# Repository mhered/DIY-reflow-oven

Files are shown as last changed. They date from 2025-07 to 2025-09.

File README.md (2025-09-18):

# DIY reflow oven

Inspired in [this video](https://www.youtube.com/watch?v=asZ1zhef8Ss) (see also the [blog post](https://www.digikey.com/en/maker/projects/how-to-build-a-solder-reflow-oven/6c52df4782084f8d97c62d1349df058f)), but I thought the BOM was too expensive. I used also [this video](https://www.youtube.com/watch?v=k9xzGO0SVg0) as inspiration, which discusses temperature curves, and includes a custom controller PCB.

Bought the following elements instead:

| Qty  | Item | Image | Description | Link | Pack Price (€) | Pack Size | Unit Price (€) | Subtotal (€) |
| ---- | --- | --- | --- | --- | --- | --- | --- | --- |
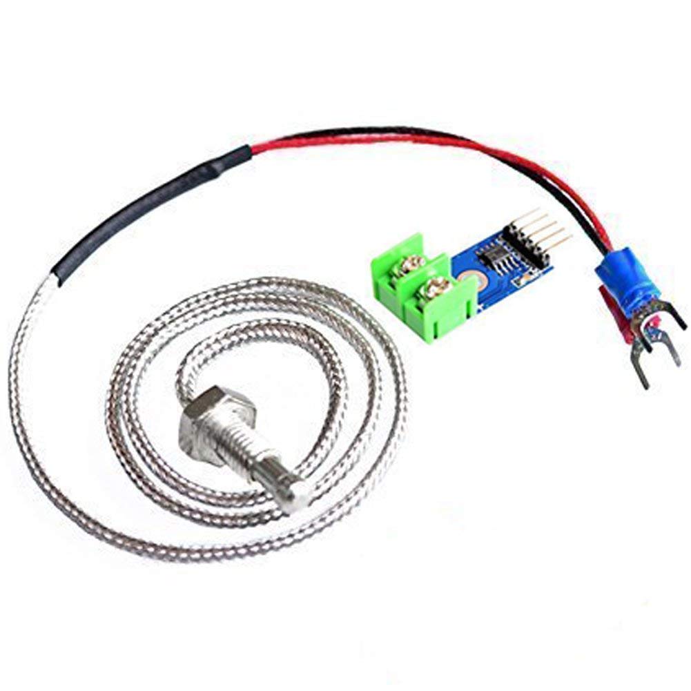
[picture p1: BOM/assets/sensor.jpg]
| 1 | [ARCELI MAX6675 module + K-type thermocouple](./BOM/sensor.md) |  | K-type thermocouple module with MAX6675, 0–600 °C range, SPI output | [Amazon](https://www.amazon.es/dp/B07MY36P9Y) | 7.99 | 1 | 7.99 | 7.99 |
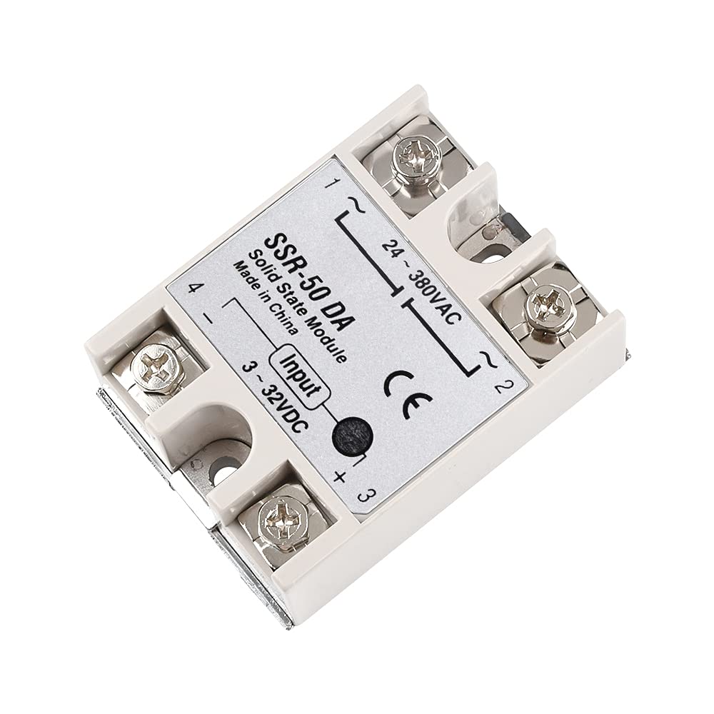
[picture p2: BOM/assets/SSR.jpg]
| 1 | [SSR-50DA Solid State Relay](./BOM/ssr.md) |  | DC 3–32 V input, AC 24–380 V output, 50A max, for heater control | [Amazon](https://www.amazon.es/dp/B08FX1DDJM) | 9.59 | 1 | 9.59 | 9.59 |
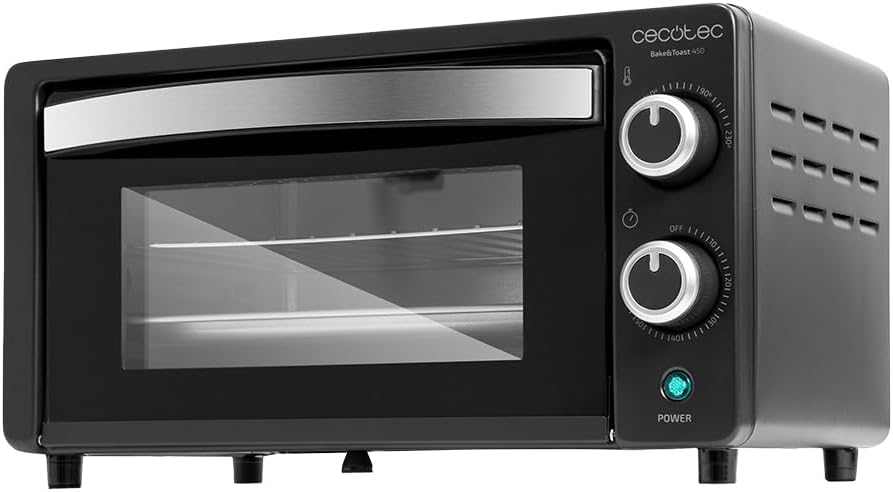
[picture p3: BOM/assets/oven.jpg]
| 1 | [Cecotec Bake&Toast 1090 Oven](./BOM/oven.md) |  | 10 L tabletop oven, 1000 W, 60 min timer, up to 230 °C | [Amazon](https://www.amazon.es/dp/B0BQ13YSVT) | 31.90 | 1 | 31.90 | 31.90 |
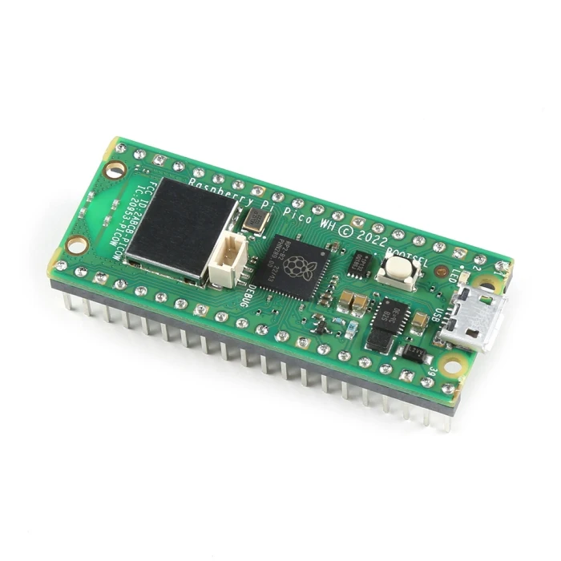
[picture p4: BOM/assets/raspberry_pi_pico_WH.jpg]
| 1 | [Raspberry Pi Pico WH](BOM/RPi_Pico.md) |  | | | | | | |
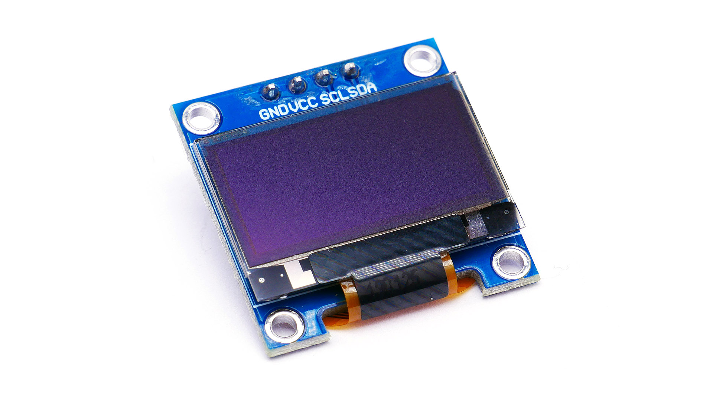
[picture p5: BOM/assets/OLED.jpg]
| 1 | [SSD1306 OLED](./BOM/OLED.md) |  | | | | | | |

I already had the Raspberry Pico WH and SSD1306 OLED screen laying around.

See [BOM/RPi_Pico.md](BOM/RPi_Pico.md) for  instructions on how to flash micropython on to the Raspberry Pi Pico and details of the pinout.

## Step 1 - Measure temperature and show it on the OLED

Target: display the temperature on the OLED using a MicroPython script

Inspired in this source video: https://www.youtube.com/watch?v=aUPvASe8D-w

### Wiring

While I wait for the thermocouple to arrive by post I am building a proof of concept using a 10K thermistor and a 10kOhms resistor from my trusted [Freenove_Ultimate_Starter_Kit_for_Raspberry_Pi](https://github.com/Freenove/Freenove_Ultimate_Starter_Kit_for_Raspberry_Pi), wired in a voltage divider configuration as shown below (actually one of the tutorials in this repo demonstrates this application).

```
3.3V --- [10kΩ] ---+--- [10K Thermistor] --- GND
                   |
                GPIO26 (ADC 0)
```

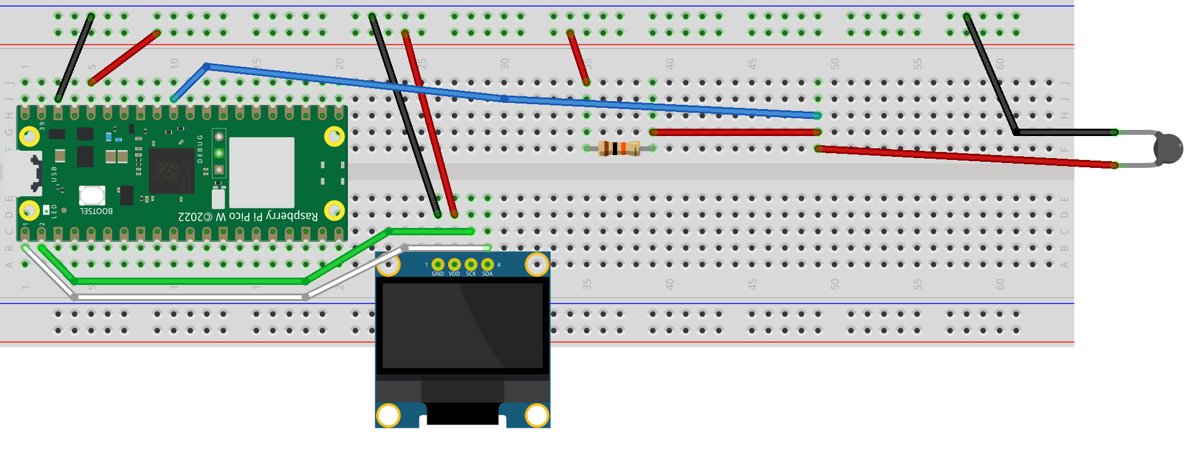
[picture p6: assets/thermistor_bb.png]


Check out the [fritzing model](./fritzing/diy_reflow_oven_v1.fzz)

### Firmware

* `main.py` - main function
* `display.py` - functions to send info to the OLED display  
* `thermistor.py` -  functions to read the sensor. Note I used a very simplified model of the variation of the thermistor's resistance with temperature using a single constant. This [Online Steinhart-Hart model coefficients calculator]( https://www.thinksrs.com/downloads/programs/therm%20calc/ntccalibrator/ntccalculator.html) provides a more accurate model but requires making R measurements at 3 known T points, which I felt was an overkill for the proof of concept.

Copy dependencies to the Pico:

* `ssd1306.py` - library to communicate with the OLED (copied from https://github.com/stlehmann/micropython-ssd1306)
* `writer.py` - an interpreter for custom fonts for the OLED  (copied from the link in the comments of this video: https://www.youtube.com/watch?v=bLXMVTTPFMs)
* `freesans20.py` - a custom large font for the OLED  (copied from the link in the comments of this video: https://www.youtube.com/watch?v=bLXMVTTPFMs)

Note: the files from https://github.com/peterhinch/micropython-font-to-py did not work for me.

## Step 2  - setup a web server over WiFi to interact from computer or phone

Profiting from the capabilities of the RPi Pico I decided to set up a local web server over Wifi to view temperature readings from a computer or phone connected to the same Wifi network as the Pico

### Firmware

* `wifi.py` : function to connect the RPi Pico to Wifi. Requires uploading to the Pico a `secrets.py` file containing the network information as follows:

```bash
SSID = "Network"
PASSWORD = "Password"
```

* `server.py` :  a very basic web server that just publishes the temperature every 2 seconds

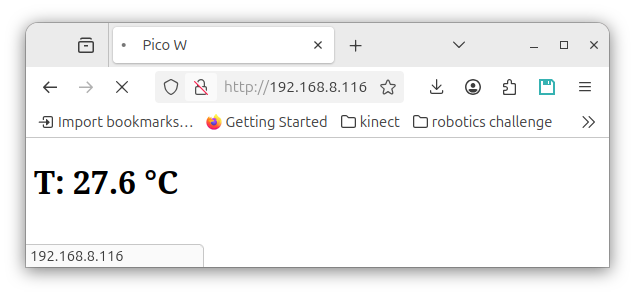
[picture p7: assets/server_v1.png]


## Step 3 - Control the heater

Next we refactor using the [Microdot](https://github.com/miguelgrinberg/microdot) framework and add a few improvements:

* Replace repeated full-page reload every 2 seconds using meta-refresh with polling a tiny JSON file using Java Script. This is more efficient, avoids page flicker and is more extensible 
* Save web page as static files (`index.html` and `style.css`) with a minimalistic, modern design
* Add `/set_target?value=XX` route to update target temperature via HTTP
* Add REST endpoint `/temperature` exposing current and target temp + heater state

* `heater.py` - contains the target temperature logic and functions to control a heater in GPIO22

Dependencies: copy the library  `microdot.py` to the pico

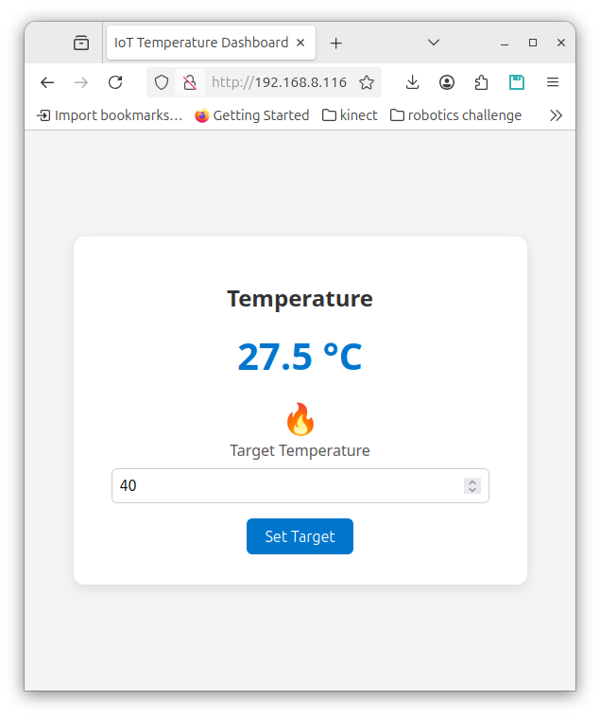
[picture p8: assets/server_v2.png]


### Wiring

In preparation to control the heater we add an LED on GPIO22

Check out the [fritzing model](./fritzing/diy_reflow_oven_v2.fzz)

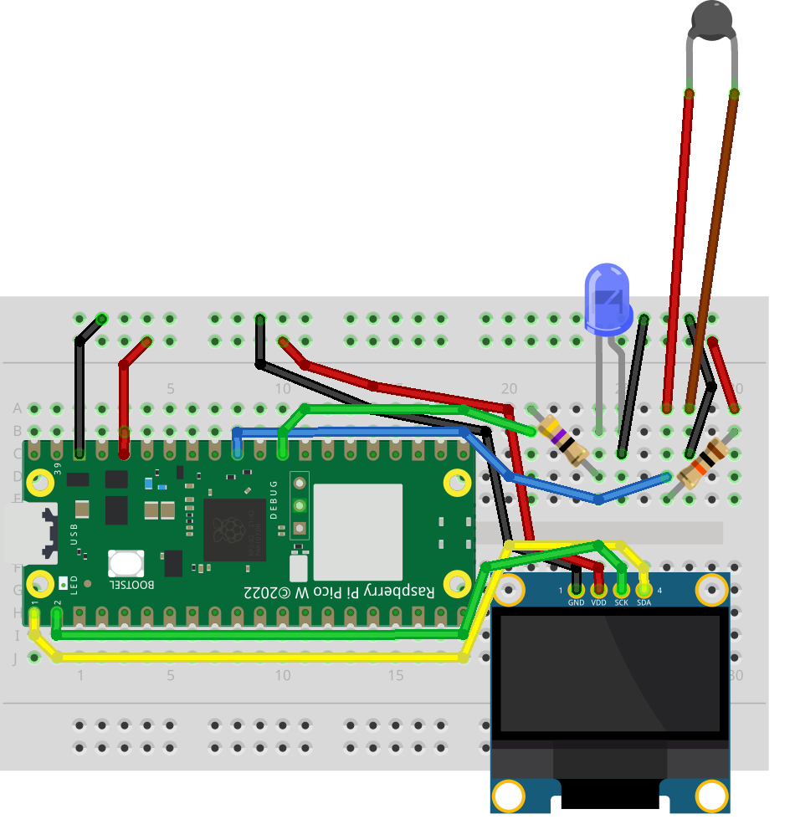
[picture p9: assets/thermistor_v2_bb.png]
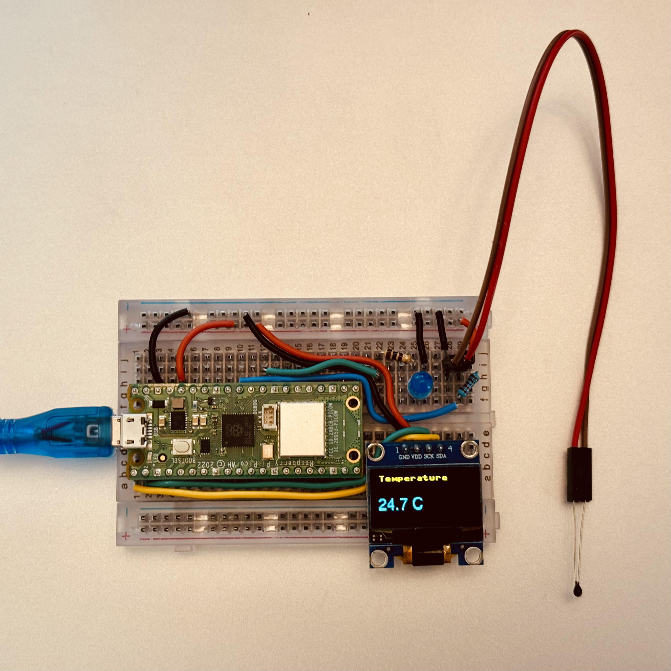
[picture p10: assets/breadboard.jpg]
|  |  |
| --- | --- |

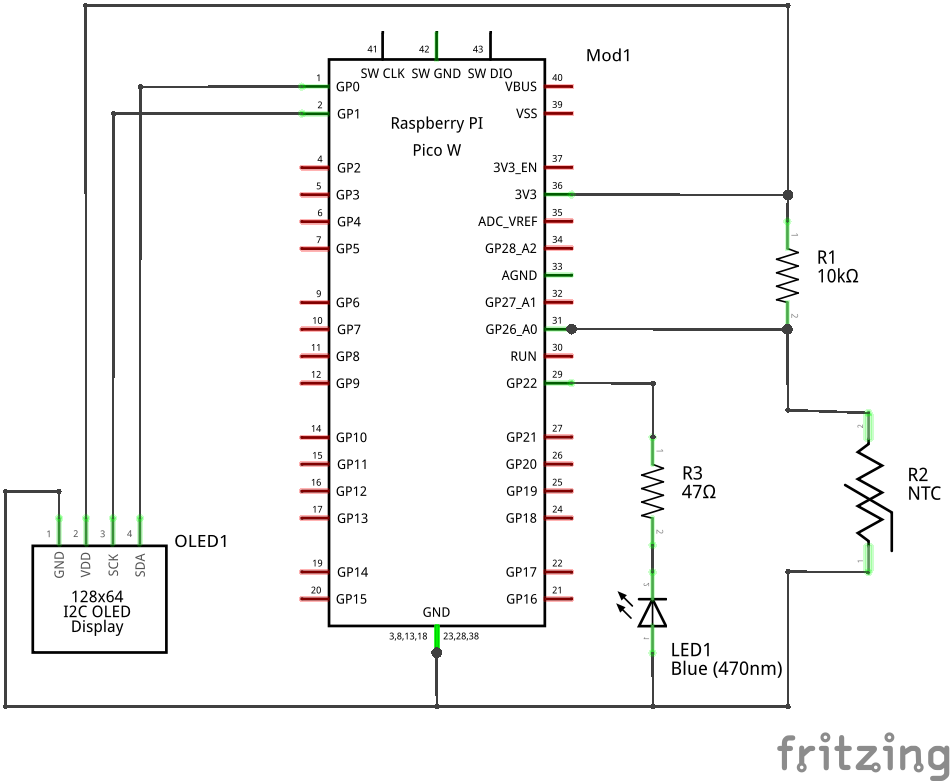
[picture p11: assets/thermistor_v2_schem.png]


## Step 4 - Temperature Profiles

Next we refactor to add support for temperature profiles and disable manual target temperature setting:

- `profile.py` - classes for multi-phase temperature control with JSON serialization
- `profile_manager.py` functions to manage profile execution, file persistence, and state tracking
- new `profiles/` folder to store temperature profiles as JSON files
  - [low_temp.json](./src/profiles/low_temp.json) profile based on [this datasheet](./assets/low_temp_solder_paste_datasheet.pdf) for Sn42Bi57Ag1 Low Temperature Solder Paste

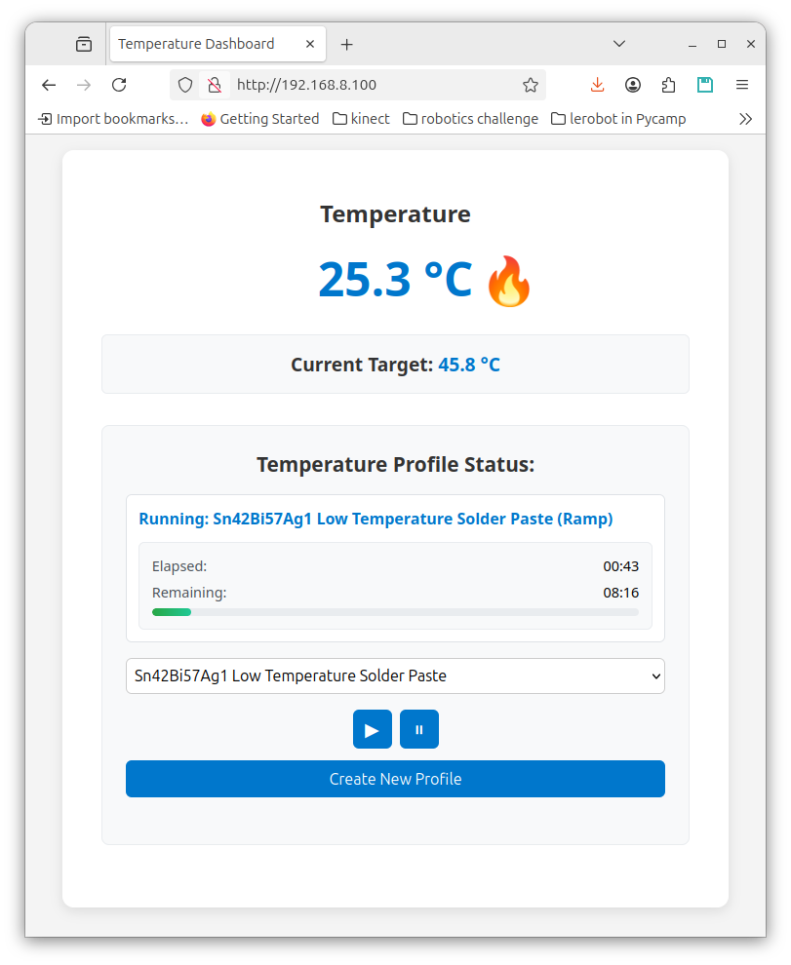
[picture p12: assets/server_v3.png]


## Step 5 - Plot temperature graphs

This is a test with simulated temperature

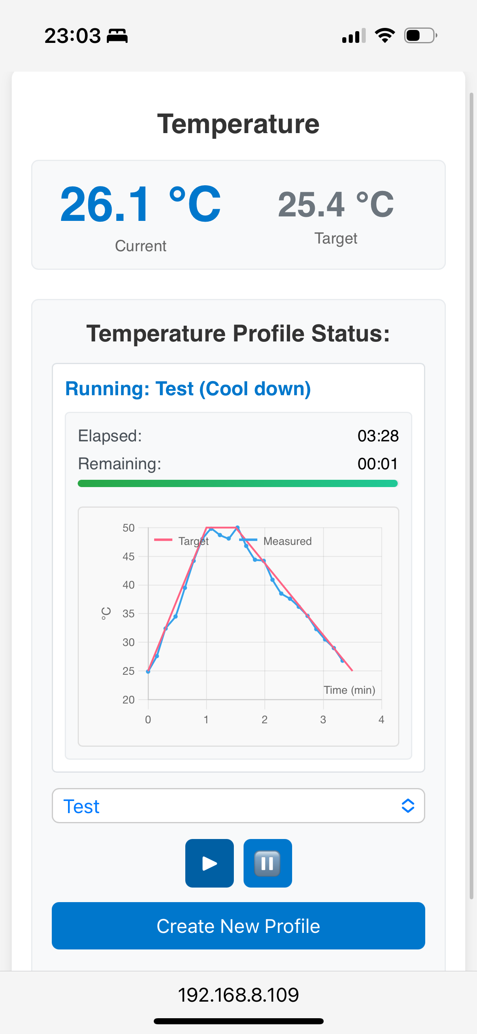
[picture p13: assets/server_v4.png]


## Step 5 - Optimize architecture

Move state logic to `ProfileManager` class, put some order in the UI, improve set of example profiles etc.

**Bulb Test 55 °C — Proof of Concept**

The graph below shows a temperature profile recorded during a full system test in a simple proof-of-concept setup. An old incandescent bulb served as the heating element, switched by the Raspberry Pi Pico via a solid-state relay connected to GPIO22 . To mimic an oven enclosure, the bulb and temperature sensor were covered with an inverted beer glass, allowing the air temperature to rise quickly to the 55 °C target.

The small ripples in the measured temperature trace reflect the heater control loop cycling the bulb on and off to follow the requested profile. Towards the end of the test, the measured temperature fell behind the target curve because heat dissipation under the glass was not fast enough to achieve the desired cooling rate.

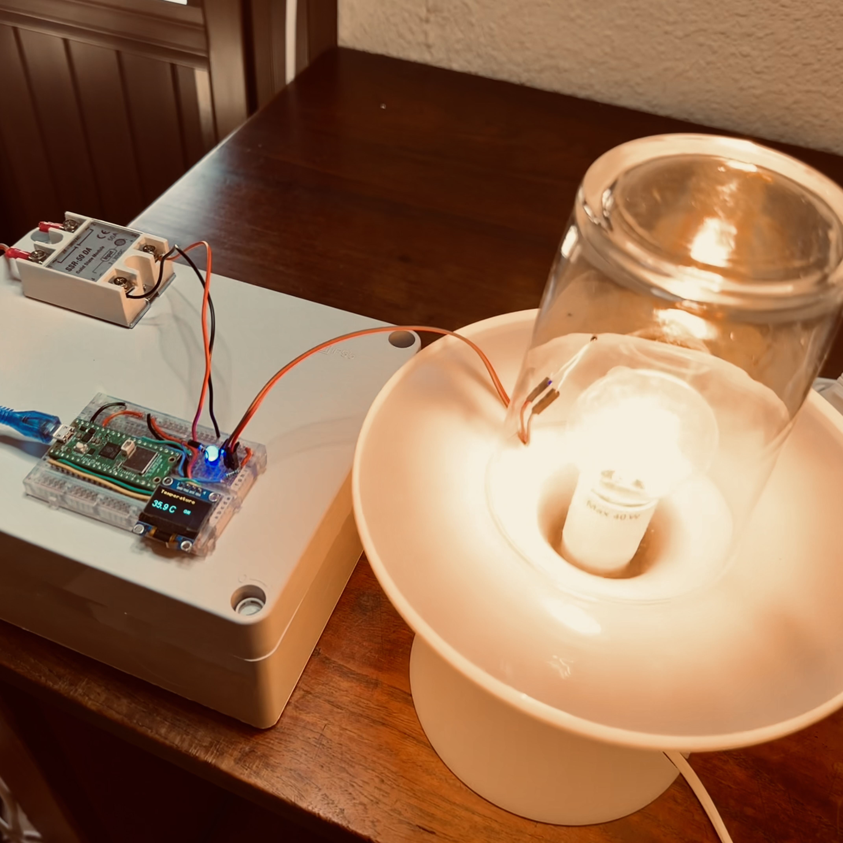
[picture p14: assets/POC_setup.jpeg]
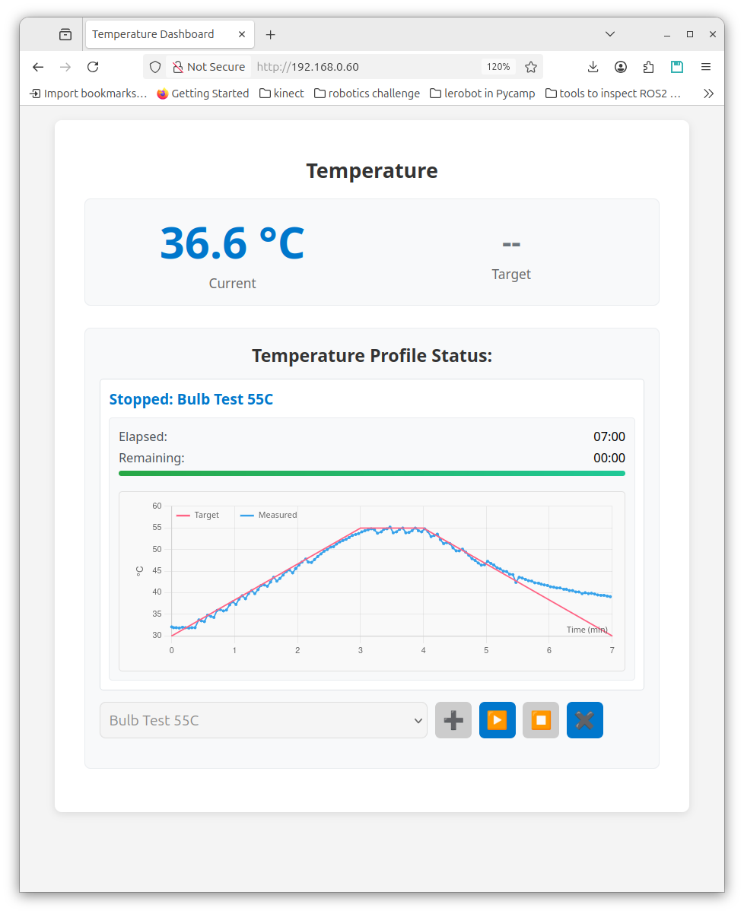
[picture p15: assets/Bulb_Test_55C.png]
|  |  |
| --- | --- |

## Step 6 - (Finally) hacking the oven for real

Two sanity checks on the Cecotec oven before we proceed:

1. Two infrared heater pieces powerful enough (1000W) to quickly heat up and cool down
2. Confirmed that if we shut down and power up again the oven it resumes working (there are no electronics that reset the timer etc). This allows us controlling the oven as we did with the incandescent bulb in the proof of concept.
3. The lower tray for removing breadcrumbs is perfect to feed the wire of the thermocouple to get temperature measurements inside the oven without the need to drill a hole or modify the oven in any way.

### Firmware

Next we need to adapt the code for the K-type thermocouple and MAX6675. Refer to [this tutorial](https://www.electroniclinic.com/raspberry-pi-pico-and-max6675-based-industrial-temperature-monitoring-system/).

## WIP

- [ ] created branch `feature/polling-improvements-WIP` with partial implementation of incremental temperature updates instead of full dumps for the graph to enable higher refresh rates without memory problems, and to configure the refresh of different elements such as the graph, measured and target temperatures, UI buttons states, etc using centralized named constants instead of magic numbers scattered throughout the code
- [ ] check also open issues
- [x] test the oven and reflow first part
- [ ] add pictures and gifs

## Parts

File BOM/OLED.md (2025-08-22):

# SSD1306 OLED



SSD1306 is a popular controller for OLED screens

resolution 128x64

Check if the I2C address is 0x3D or 0x3C

Power consumption: according to https://bitbanksoftware.blogspot.com/2019/06/how-much-current-do-oled-displays-use.html,  for text (~50% pixels at 100%) is around 10mA so at 5V is ~50mW 

### Wiring the SSD1306 OLED to the Pico

I2C communication requires only 4 pins: GND, VCC, SDA, SCL 

| OLED Pin | Connect To Pico | Pico Pin Number | Function |
| --- | --- | --- | --- |
| `VCC` | 3.3V | Pin 36 | Power |
| `GND` | GND | Pin 38 or 3 | Ground |
| `SCK` | GP1 | Pin 2 | I²C0 SCL |
| `SDA` | GP0 | Pin 1 | I²C0 SDA |

## Controlling the OLED with Micropython

* `ssd1306.py` - library to communicate with the OLED (copied from https://github.com/stlehmann/micropython-ssd1306)

## Large fonts in Micropython

Ref. https://github.com/peterhinch/micropython-font-to-py 

* `writer.py` - an interpreter for custom fonts for the OLED
* `freesans20.py` - a custom large font for the OLED 

Note: the files from https://github.com/peterhinch/micropython-font-to-py did not work for me, so I copied them instead from the link in the comments of this video: https://www.youtube.com/watch?v=bLXMVTTPFMs

## Useful references

* A tool to design pixelart: https://www.pixilart.com/



* Check out wokwi online emulator https://wokwi.com/ for Arduino, ESP32 and Raspberry Pi Pico and animation maker https://animator.wokwi.com/

  Using the wokwi emulator I made code to display distance measurements, check:

  * parking_sensor: https://wokwi.com/projects/380210366387901441
  * distance_measurement: https://wokwi.com/projects/380210201131269121

* Check out also this image2cpp tool to make byte arrays from images and viceversa: http://javl.github.io/image2cpp/

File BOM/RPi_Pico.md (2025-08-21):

# Raspberry Pi Pico WH



### RPi Pico WH pinout



### Flashing MicroPython onto the Pico

I used [Thonny](https://thonny.org/) (a python IDE for beginners with great MicroPython integration). 

1. Install and run:

```bash
$ sudo apt install thonny
$ thonny
```

2. Plug the RPi Pico in boot mode: while holding down the **BOOTSEL** button on the RPi Pico, connect the USB cable to your computer, and a new drive will appear: **RPI-RP2**

3. flash MicroPython on the RPi Pico: 
   1. Go to **Tools** > **Options**
   2. In the **Interpreter** tab select **"MicroPython (Raspberry Pi Pico)"** in the dropdown and click **"Install or update MicroPython"**. Thonny will detect the RPi Pico automatically. 
   3. Select variant **"Raspberry Pi Pico W / Pico WH"**. It will download and flash the **MicroPython UF2 file** automatically.
   4. Click **Install** and wait for it to finish
   5. After install, the RPi Pico will reboot and connect directly to Thonny — you’ll see the MicroPython REPL (>>>) at the bottom.

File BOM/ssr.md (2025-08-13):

# diymore SSR-50 DA Solid State Relay

See: https://www.amazon.es/dp/B08FX1DDJM



Dimensions : ‎ 9,3 x 7,2 x 2,4 cm; 100 g
Manufacturer ‏ : ‎ diymore
ASIN ‏ : ‎ B08FX1DDJM
Manufacturer Reference ‏ : ‎ D010158

DC in: 3-32V DC

AC out: 24-380 VAC up to 50A

## References

Datasheets of similar products can be found [online](https://www.alldatasheet.com/datasheet-pdf/view/1940532/ETC/SSR50DA.html). I saved a local backup [here](../assets/SSR-40DA_datasheet.PDF).

A good reference: [Solid State Relay guide by phidgets](https://www.phidgets.com/docs/Solid_State_Relay_Guide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) 

According to **Practical Electronics by Inventors, sections 3.4.1 and 3.4.2** protecting tyhe Piuco with a diode seems unnecessary for my application, but also harmless. I decided to install a 1N4007. 

On the other hand it may be a good idea to add also a [plastic cover](https://es.aliexpress.com/item/1005002904930594.html) and a [heat sink]()

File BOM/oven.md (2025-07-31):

#   Cecotec Bake&Toast 1090 Oven

  

10 L tabletop oven, 1000 W, 60 min timer, up to 230 °C 

Source: https://www.amazon.es/dp/B0BQ13YSVT

Color	Negro
Dimensiones del producto	27f. x 37an. x 20,5al. cm, 2.77kg
Función especial	Termostato ajustable, temporizador
Tipo de control	Control por botones
Componentes incluidos	Bandeja para hornear, parrilla y asa con pinzas

Número de modelo	‎03816

[Manuals (PDF)](Cecotec_bake&toast_1090_manuals.pdf)

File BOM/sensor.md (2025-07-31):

#  ARCELI MAX6675 module + K-type thermocouple

  K-type thermocouple module with MAX6675, 0–600 °C range, SPI output  Source: https://www.amazon.es/dp/B07MY36P9Y

## Specs

**Manufacturer:** ARCELI  
**ASIN:** B07MY36P9Y  
**Dimensions:** 1.5 × 1.5 × 1.5 cm; 20 g

**Included:**

- 1× Sainsmart MAX6675 breakout module  
- 1× Sainsmart K-type thermocouple probe  
- 1× Sainsmart DuPont jumper cable set  

### MAX6675

- **Power Supply Voltage:** 3 V – 5 V DC  
- **Current Consumption:** 50 mA  
- **Interface Pins:** `GND`, `VCC`, `SCK`, `CS`, `SO` (SPI communication)  
- **Module Size:** 25 mm × 15 mm  
- **ESD Protection:** 2000 V signal-level protection  
- **Operating Temperature (board):** −20 °C to +85 °C  
- **Cold-Junction Compensation:** Built-in; automatically senses the temperature at the chip's own terminals and adjusts the thermocouple reading  
- **Break Detection:** Built-in thermocouple disconnection detection  

### Sensor

- **Thermocouple Type:** K-Type (nickel-chromium/nickel-alumel)  
- **Measurement Range:** 2 °C to 600 °C  
- **Temperature Resolution:** 0.25 °C

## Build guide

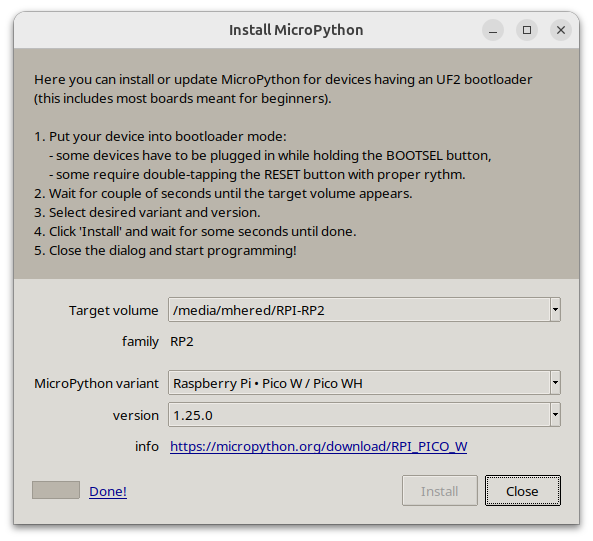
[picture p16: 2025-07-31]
assets/install_micropython.png

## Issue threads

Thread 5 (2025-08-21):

Add support for K-type thermocouple with MAX6675 module

mhered, 2025-08-21:
Ref. https://www.electroniclinic.com/raspberry-pi-pico-and-max6675-based-industrial-temperature-monitoring-system/

Closed 2025-08-22.

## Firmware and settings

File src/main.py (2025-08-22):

import random
import time

from display import Display
from server import WebServer

from thermistor import Thermistor
from simulated_sensor import SimulatedSensor
from max6675 import MAX6675
from machine import Pin

from heater import Heater
from wifi import connect
from profile import set_profile_debug

# Debug configuration - set to True to enable verbose profile logging
DEBUG_MODE = False  # Change to True for debug output
set_profile_debug(DEBUG_MODE)


# choose type of temperature sensor

class SensorType:
    THERMISTOR = 1
    MAX6675 = 2
    SIMULATED = 3

sensor_type = SensorType.MAX6675

# initialize temperature sensor

if sensor_type == SensorType.SIMULATED:
    simulated_sensor = SimulatedSensor()
elif sensor_type == SensorType.THERMISTOR:
    SENSOR_PIN = 26  # 26 to use a physical sensor
    thermistor_sensor = Thermistor(pin=SENSOR_PIN)
elif sensor_type == SensorType.MAX6675:
    sck = Pin(13, Pin.OUT) # orange cable
    cs = Pin(14, Pin.OUT) # yellow cable
    so = Pin(15, Pin.IN) # green cable
    max6675_sensor = MAX6675(sck, cs , so)

# initialize heater controller
HEATER_PIN = 22 # 22 to use a physical heater, None to simulate
HYSTERESIS = 1.0
MIN_TARGET_TEMP = 0.0
MAX_TARGET_TEMP = 300.0
INITIAL_TARGET_TEMP = None  # Start with no target (heater off)

heater = Heater(pin=HEATER_PIN,
                hysteresis=HYSTERESIS,
                min_temp=MIN_TARGET_TEMP,
                max_temp=MAX_TARGET_TEMP,
                target_temp=INITIAL_TARGET_TEMP)

# Connect to Wi-Fi
ip_address = connect()

# initialize Display
display = Display()

# Confirm it's working
display.show_message("Online at:", ip_address)

# Start web server
server = WebServer(heater)

time.sleep(5)

# Time to wait between temperature updates
WAIT = 1 			# sec

# Main loop
while True:
    if sensor_type == SensorType.SIMULATED:
        # Simulate temperature reading
        temperature = simulated_sensor.simu_temp(heater.is_on)
    elif sensor_type == SensorType.THERMISTOR:
        # Read temperature from thermistor
        temperature = thermistor_sensor.read_temp()
    elif sensor_type == SensorType.MAX6675:
        # Read temperature from MAX6675
        temperature = max6675_sensor.read()

    # Use heater class to control heating logic - heater now manages its own target
    # Check if profile manager has an active profile and update target accordingly
    profile_target = server.update_profiles()
    if profile_target is not None:
        # Profile is active, use profile target
        heater.set_target_temp(profile_target)
    else:
        # No profile active, heater stays off
        heater.set_target_temp(None)

    heater_on = heater.set_state(temperature)

    # Update current temperature and heater state
    
    # in OLED display
    display.show_temp("Temperature", temperature, heater_on)
    
    # in web server
    server.serve_temperature_once(temperature)
    server.serve_heater_state_once(heater_on)

    # in stdout
    print("Temp: {:.2f} C".format(temperature))

    time.sleep(WAIT)

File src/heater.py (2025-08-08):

"""
Heater control class for DIY reflow oven
Handles heater logic with support for simple on/off control
and extensible for future PID/hysteresis implementations
"""

class Heater:
    def __init__(self, pin=None, 
                 hysteresis=1.0,
                 min_temp=0.0, 
                 max_temp=300.0,
                 target_temp=None):
        """
        Initialize heater controller
        
        Args:
            pin: GPIO pin for heater control (if using physical pin) - default None (simulated)
            hysteresis: Temperature difference for hysteresis control (°C) - default 1.0
            min_temp: Minimum temperature limit (°C) - default 0.0
            max_temp: Maximum temperature limit (°C) - default 300.0
            target_temp: Initial target temperature (°C) - default None (heater off)
        """
        self.pin = pin
        self.hysteresis = hysteresis   
        self.min_temp = min_temp
        self.max_temp = max_temp
        self.target_temp = target_temp

        self.is_on = False
        self.last_state = False

        # Initialize GPIO if pin is provided
        if self.pin:
            try:
                from machine import Pin
                self.heater_pin = Pin(self.pin, Pin.OUT)
                self.heater_pin.off()
            except ImportError:
                print("Warning: GPIO not available, heater will be simulated")
                self.heater_pin = None
        else:
            self.heater_pin = None
    
    def set_state(self, current_temp, target_temp=None):
        """
        Update heater state based on current and target temperatures
        Uses simple hysteresis control to prevent rapid on/off cycling
        
        Args:
            current_temp (float): Current temperature reading
            target_temp (float): Optional override for target temperature.
                                If None, uses the heater's stored target_temp
                                If target_temp is None, heater stays off
            
        Returns:
            bool: True if heater should be on, False otherwise
        """
        # Use provided target or fall back to stored target
        if target_temp is None:
            target_temp = self.target_temp
        
        # If no target is set, keep heater off
        if target_temp is None:
            self.is_on = False
            self._set_physical_state(self.is_on)
            return self.is_on
        
        # Simple hysteresis control
        if not self.is_on:
            # Turn on if temperature is below target minus hysteresis
            if current_temp < target_temp - self.hysteresis:
                self.is_on = True
        else:
            # Turn off if temperature reaches target (no overshoot allowed for safety)
            if current_temp >= target_temp:
                self.is_on = False
        
        # Apply the state to physical hardware
        self._set_physical_state(self.is_on)
        
        return self.is_on
    
    def _set_physical_state(self, state):
        """Set the physical heater state"""
        if self.heater_pin:
            if state:
                self.heater_pin.on()
            else:
                self.heater_pin.off()
        
        # Log state changes
        if state != self.last_state:
            print("Heater {}".format('ON' if state else 'OFF'))
            self.last_state = state
      
    def get_state(self):
        """Get current heater state"""
        return self.is_on
    
    def emergency_stop(self):
        """Emergency stop - immediately turn off heater"""
        self.is_on = False
        self._set_physical_state(False)
        print("EMERGENCY STOP: Heater turned off")
    
    def set_hysteresis(self, hysteresis):
        """
        Set hysteresis value for temperature control
        
        Args:
            hysteresis (float): Temperature difference in °C
        """
        self.hysteresis = max(0.1, hysteresis)  # Minimum 0.1°C hysteresis
        print("Hysteresis set to {}°C".format(self.hysteresis))

    def set_target_temp(self, value):
        """Set target temperature with validation"""
        if value is None:
            if not self.target_temp is None: # reduce redundant debug messages
                self.target_temp = None
                print("Target temperature disabled (heater off)")
            return {'status': 'ok', 'target': None}
        elif self.min_temp <= value <= self.max_temp:
            self.target_temp = value
            print("Target temperature set to {}°C".format(self.target_temp))
            return {'status': 'ok', 'target': self.target_temp}
        else:
            return {'status': 'error', 'message': 'Target out of range ({}-{}°C)'.format(self.min_temp, self.max_temp)}, 400
    
    def get_target_temp(self):
        """Get current target temperature"""
        return self.target_temp
    
    def get_temp_limits(self):
        """Get temperature limits"""
        return {'min': self.min_temp, 'max': self.max_temp}
    
    def get_status(self):
        """Get complete heater status"""
        return {
            'target_temp': self.target_temp,
            'is_on': self.is_on,
            'hysteresis': self.hysteresis,
            'min_temp': self.min_temp,
            'max_temp': self.max_temp
        }

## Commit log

2025-07-31 Implement Display class and a stump of WebServer class
    - Wrap OLED display logic in a Display class (display.py)
    - Implement WebServer class (server.py) - will use to serve temperature via HTTP
    - Clean up main.py to use modular components
2025-07-31 Fix web server autorefresh and refactor sensor reading into Thermistor class
    - in server.py - improve server responsiveness and add autorefresh
    - use uselect.poll() to avoid blocking
    - set 2 sec auto-refresh via <meta> tag
    - new thermistor.py - a reusable Thermistor class
    - in main.py - refactor to use new class
    [main.py, server.py, thermistor.py]
2025-08-03 Move Fritzing assets to ./fritzing/
    [thermistor.fzz]
2025-08-03 Improve webserver with microdot framework
    Improvements:
    * replace repeated full-page reload every 2 seconds
    using meta-refresh with polling JSON using Java Script.
    This is more efficient, avoids page flicker and is more extensible
    * save web page as static files (`static/index.html` and `static/style.css`),
    add a minimalistic modern design
    * enable updating target temperature via webUI - `/set_target?value=XX` route
    * expose current and target temp + heater state - route `/temperature`
    [server.py]
2025-08-04 Add heater control and simulated temperature mode
    - new `heater.py` - new `Heater` class to control a heater on
    `GPIO 22` based on temperature
    - in `thermistor.py` - add simulation mode: optional `pin=None` to
    simulate temperature with random noise and heating/cooling rates
    - in `server.py`- update `WebServer` class to expose and sync real
    heater state via JSON API
    - in `main.py`- update loop to support both real and simulated
    sensor data
    - in `display.py`- add heater state indicator "ON"
    - in `index.html`and `style.css` - modify layout so heater state
    indicator appears to the right of the temperature without
    disrupting the layout of other elements
    [display.py, heater.py, main.py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]
2025-08-04 Refactor to move `target_temp` logic to `Heater` class
    - in `heater.py` - make `Heater` class the single source of Truth:
    - Add `get_target_temp()` and `get_temp_limits()` methods
    - Enhance `set_target_temp()` with better validation and logging
    - Modify `set_state()` to optionally use its own `target_temp`
    - Add `get_status()` for complete heater status
    - in `server.py` - `Server` class delegates to `Heater`:
    - Remove `target_temp` storage - now gets it from heater
    - Constructor now takes `heater`parameter instead of `initial_target`
    - `/temperature` endpoint gets target from `heater.get_target_temp()`
    - Improve error messages
    * in `main.py`:
    - Initialize `Heater` with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
    [display.py, heater.py, main.py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]
2025-08-04 Replace f-strings for MicroPython compatibility
    [heater.py]
2025-08-04 Initialize Heater class with all parameters
2025-08-04 Add support for temperature profiles
    - in `main.py` - delegate on active profile to update the target
    temperature
    - in `server.py` - add profile manager integration, extend
    `temperature` endpoint with profile status, add profile management
    API endpoints (`/profiles`, `/profile/start`, `/profile/stop`), maintain
    backward compatibility with feature flag
    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
2025-08-04 Fix JSON serialization bug
    [profile.py]
2025-08-05 Fix bugs in Profile-based control, disable Manual target setting
    - in `heater.py` – disable heater when temperature target is `None`
    - in `main.py` – default heater to off, implement Newton’s ambient
    cooling law in simulated temperature
    - in `profile.py` – fix bugs in JSON filename handling, clean up
    serialization, remove support for climb rate in `TemperaturePhase`
    (only duration-based)
    - in `profile_manager.py` – fix bug saving profiles, improve debug
    messages, update calculation of elapsed time when profile is active
    - in `server.py` – remove support for manual setting of target
    temperature, default temp target to `None` when a profile stops,
    add `/profile/create`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
    [heater.py, main.py, profile.py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]
2025-08-08 Fix profile dropdown refresh bug, add structured debugging system
    - in `.gitignore` - add `__pycache__/` to exclusion list
    - in `heater.py` - prevent repeated "Target temperature disabled"
    messages
    - in `main.py`- call `set_profile_debug()` with `DEBUG_MODE` flag to
    enable/disable verbose logging
    - in `profile.py`- recursion workaround and structured logging
    * Implement manual object creation using `object.__new__()`in
    `from_dict()` method to bypass weird MicroPython recursion
    bug in `__init__`
    * improve error handling with structured logging of meaningful
    error messages
    * Add `os.sync()` calls to ensure proper file saving
    * throw warning if temperature profile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
    [heater.py, main.py, profile.py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]
2025-08-08 Improve notes, add figures
    [thermistor_v2.fzz]
2025-08-08 Update fritzing model
    [thermistor_v2.fzz]
2025-08-10 Basic graph of temperature profile
2025-08-15 Major refactor to move state logic to class `ProfileManager`
    - in `profile_manager.py`- completely refactor `ProfileManager`class to centralize management
    of 3 states: 1 - No Profile Active, 2 - Profile Active & Stopped, 3 - Profile Active & Running
    - Add NEW 3-state variables: `active_profile_name`, `is_running`, `temperature_data`
    - Add state transition methods: `activate_profile()`, `deactivate_profile()`
    - Add new profile control methods: `start_active_profile()`, `stop_active_profile()`
    - Add temperature data collection: `add_temperature_reading()`, `get_temperature_data()`
    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
2025-08-15 Improve the set of example profiles
    - in `src/profiles/` folder - tweak example profiles and give them more descriptive
    names:
    - new `Bulb_Test_55C.json` - a profile to check the proof of concept using an
    incandescent bulb to increase temperature up to 55C
    - `hold_33.json` renamed `Manual_Test_33C.json` - a profile to check the logic
    of the heater warming the sensor between your fingers up to 33C
    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
2025-08-21 Create dedicated OLED and RPi_Pico notes files in BOM/ folder
2025-08-21 Improve notes, add links to fritzing models
    [diy_reflow_oven_v1.fzz, diy_reflow_oven_v2.fzz]
2025-08-22 Refactor support for multiple sensor types, add support for MAX6675
    - new `max6675.py` - driver for thermocouple with MAX6675 module
    * Implement SPI protocol for reading temperature from MAX6675
    * Add error detection and measurement timing
    - new `simulated_sensor.py` - implement new `SimulatedSensor` class
    * Provide configurable ambient, noise, heating, and cooling parameters
    * Implement `simu_temp()` to simulate temperature readings
    - in `thermistor.py` - Set default pin to 26
    * Change `__init__` default pin argument from `None` to `26`
    - in `main.py` - Refactor to support multiple sensor types and modularize
    * Add `SensorType` class for sensor selection
    * Add support for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
    [main.py, simulated_sensor.py, thermistor.py]
2025-08-22 Commit unsaved notes on BOM/OLED.md
2025-08-22 Fix image link in BOM/OLED.md
2025-08-27 Fix bug #6 that prevented loading profiles with long names
    - in `profile.py`- Add name shortening and streamline debug messages
    * Add `_make_short_name` to clip names to 20 chars
    * Store original name in `display_name`
    * Improve debug messages
    * Simplify profile validation and error handling
    - in `profiles/` folder - formatting improvements to profile JSON files
    [profile.py]
